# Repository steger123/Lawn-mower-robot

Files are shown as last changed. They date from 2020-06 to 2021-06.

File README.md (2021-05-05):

# Lawn-mower-robot


## The main purpose of the project:

**Create a general, affordable, computational platform, which can be used for small & medium size robots.**

The navivation can be: fully maunal, semi and full autonomouse.
The mechanical side not restricted.
As the project progressing and evolving **You can learn more and more**, **and of course, have the designs and codes for free.**

## Software:

### BASE:
Mission Planner: C#
https://github.com/steger123/Lawn-mower-robot/tree/master/03_Software%20codes/02_C%23_Mission%20planner

### ROVER:
Main MCU : C++ (Arduino)
https://github.com/steger123/Lawn-mower-robot/tree/master/03_Software%20codes/01_C%2B%2B_Arduino/01_Rover/Test_Motor_v12

AI: Python (Jetson NANO)
https://github.com/steger123/Lawn-mower-robot/tree/master/03_Software%20codes/03_Python_AI_Jetson%20Nano/01_myOpenCV

### ROVER Electronic boards:
1. Arduino MEGA later Shieldbuddy TC375 (It has 3 cores !)
2. Custom made shield, sitting on the Arduino MEGA to have enough space for connectors (4xseial, 4xSPI, 3xI2C, buttons, 3xultrasonic sensos, volt & ampere meter etc.).
3. GPS: 2 x GNSS modules with RTK / Xbee. More here: https://github.com/steger123/Lawn-mower-robot/issues/8
5. Base's RTK: simpleRTK2Blite from Ardusimple or GPS Development Tools SparkFun GPS-RTK-SMA Breakout - ZED-F9P
6. Rovers RTK: RTK+INS simpleRTK2B-F9R V3 from Ardusimple or SparkFun Accessories SparkFun GPS-RTK Dead Reckoning Breakout - ZED-F9R
7. Motor controllers: 2x DC
8. RF radio: for additional Base to Rover and back communication (remote controll, getting sensor date from rover to mission control software).
9. Jetson Nano with normal webcam. Communicating via serial port to the MEGA (detect plant diseases, following plant line)
10. Sensors on the shield (utlrasonoic distance, battery volt, curret mesuring, rain etc.)

## Body:
As you like. In scouting for example: 1m x 1m x 0.5m

## Wheels:
As you like. In scouting for example: driven 280 mm in diamteter + castor wheels.
it can be smoot like a bicycle or thick lugs like on a tractor tire (good grippong during scouting on the field).

## Engine/motor:
As you like. In scouting for example: 2x 50W DC motors with encoders. 50 rpm

## Transmission:
As you like. In scouting for example: plannetary gerabox.

## Collaboration (software, electronic hardware, new PCB/shield, mechanical parts etc.):
If You like to join, please contact me:
andras.steger@protonmail.com

More information:
https://github.com/steger123/Lawn-mower-robot/wiki

## Latest news:
https://twitter.com/StegerAndras

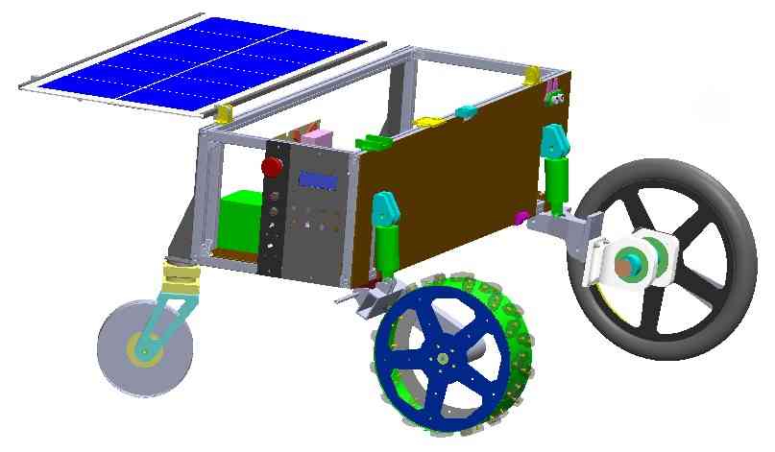
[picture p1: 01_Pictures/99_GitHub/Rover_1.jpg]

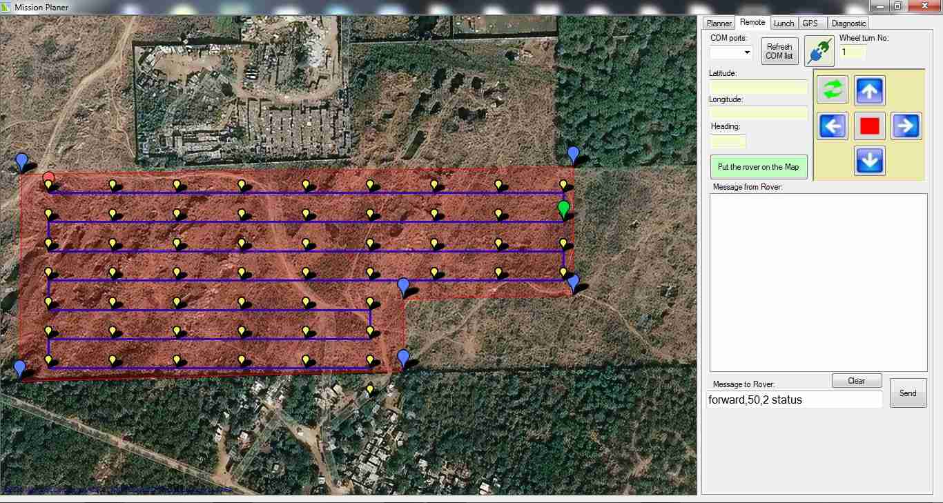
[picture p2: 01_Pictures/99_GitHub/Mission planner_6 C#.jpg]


Custom robot rover shield for Arduino MEGA or ShieldBuddy TC375:
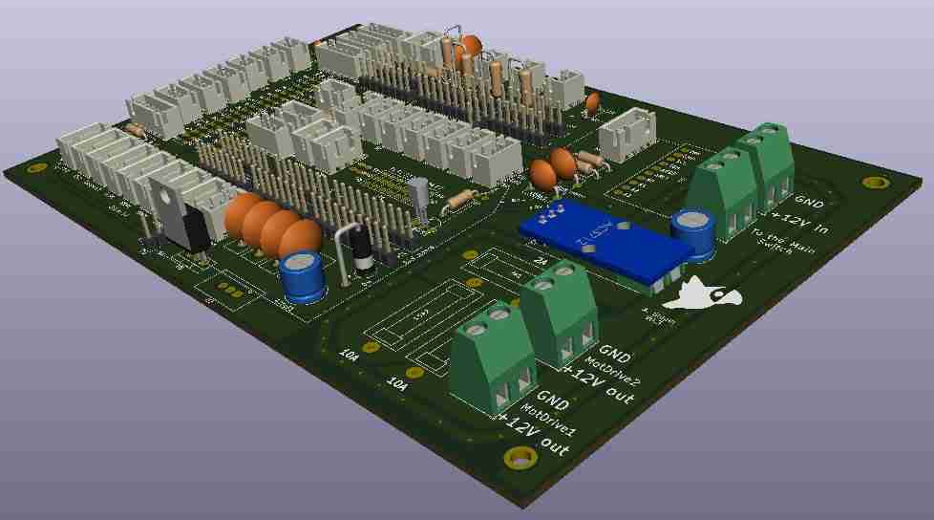
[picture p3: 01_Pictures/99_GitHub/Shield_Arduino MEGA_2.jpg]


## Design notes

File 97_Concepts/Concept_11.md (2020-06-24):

# Lawn-mower-robot
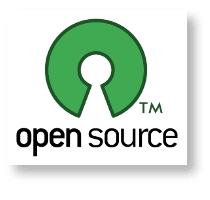
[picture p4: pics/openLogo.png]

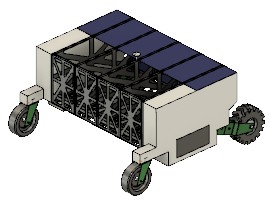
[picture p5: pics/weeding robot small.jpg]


Project parameters:

## Body:
1. Size: approx. 600x400mm
2. Total weight: max 20 kg.
3. Material: 20x20 aluminum profiles for less weight and versatility.
https://robokits.co.in/mechanical-parts/aluminium-profile-accessories/black-anodized-industrial-aluminum-alloy-2020b-profile
4.	Design platform: in AutoCAD Fusion 360

## Driven Wheels (2 pcs):
1.	Size: 10-13 inch
2.	Weight: max. 500 g/pc
3.	Material: 3D printed from PETG (PLA have less strength & fatigue).
4.	Design platform: in AutoCAD Fusion 360

## Not driven wheels (2 pcs):
1.	Caster wheel.

## Transmission:
1.	Motor: 2 pcs ODrive with encoder (DUAL SHAFT MOTOR - D6374 150KV)
https://odriverobotics.com/shop/odrive-custom-motor-d6374-150kv
2.	Motor Driver: 1pcs ODrive v3.6
https://odriverobotics.com/shop/odrive-v36
3.	Gear box with timing spokets and belt.

## Electronic:
1.	Jetson Nano
2.  Camera
3.	Route planning: GPS and real kinematics

## Software:
1. Python
2. TensorFlow, PyTorch
The software have to ensure object recognition, obstacle avoidance and route planning.

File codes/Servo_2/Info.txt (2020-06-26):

https://www.youtube.com/watch?v=9jcEwn7GzNs
https://github.com/adafruit/Adafruit_Python_PCA9685

To install the library from source (recommended) run the following commands
 on a Raspberry Pi or other Debian-based OS system:
Enable I2C on RP ! ($ sudo raspi-config)

sudo apt-get install git build-essential python-dev
cd ~     #may be not reqired
git clone https://github.com/adafruit/Adafruit_Python_PCA9685.git
cd Adafruit_Python_PCA9685
sudo python setup.py install    # for python 2
sudo python3 setup.py install	# for python 3

Program:
# Simple demo of of the PCA9685 PWM servo/LED controller library.
# This will move channel 0 from min to max position repeatedly.
# Author: Tony DiCola
# License: Public Domain
from __future__ import division
import time

# Import the PCA9685 module.
import Adafruit_PCA9685

# Uncomment to enable debug output.
#import logging
#logging.basicConfig(level=logging.DEBUG)

# Initialise the PCA9685 using the default address (0x40).
pwm = Adafruit_PCA9685.PCA9685()

# Alternatively specify a different address and/or bus:
#pwm = Adafruit_PCA9685.PCA9685(address=0x41, busnum=2)

# Configure min and max servo pulse lengths
servo_min = 150  # Min pulse length out of 4096
servo_max = 600  # Max pulse length out of 4096

# Helper function to make setting a servo pulse width simpler.
def set_servo_pulse(channel, pulse):
    pulse_length = 1000000    # 1,000,000 us per second
    pulse_length //= 60       # 60 Hz
    print('{0}us per period'.format(pulse_length))
    pulse_length //= 4096     # 12 bits of resolution
    print('{0}us per bit'.format(pulse_length))
    pulse *= 1000
    pulse //= pulse_length
    pwm.set_pwm(channel, 0, pulse)

# Set frequency to 60hz, good for servos.
pwm.set_pwm_freq(60)

print('Moving servo on channel 0, press Ctrl-C to quit...')
while True:
    # Move servo on channel O between extremes.
    pwm.set_pwm(0, 0, servo_min)
    time.sleep(1)
    pwm.set_pwm(0, 0, servo_max)
    time.sleep(1)

# Move servo on channel 1 between extremes.
    pwm.set_pwm(1, 0, servo_min)
    time.sleep(1)
    pwm.set_pwm(1, 0, servo_max)
    time.sleep(1)

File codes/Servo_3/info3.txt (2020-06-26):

https://learn.adafruit.com/16-channel-pwm-servo-driver?view=all

#sudo apt-get install ...
sudo pip install Adafruit-Blinka
sudo pip install adafruit-circuitpython-pca9685
sudo pip install adafruit-circuitpython-servokit

Program:
# Simple test for a standard servo on channel 0 and
# a continuous rotation servo on channel 1.

import time
from adafruit_servokit import ServoKit
 
# Set channels to the number of servo channels on your kit.
kit = ServoKit(channels=16)  # 8 for FeatherWing, 16 for Shield/HAT/Bonnet.
 
kit.servo[0].angle = 180      #Set the angle to 180, one extreme of the range
kit.continuous_servo[1].throttle = 1      #start the continuous rotation servo connected to channel 1 to full throttle forwards
# kit.continuous_servo[1].throttle = 0.5 To set half throttle, use a decimal
time.sleep(1)
kit.continuous_servo[1].throttle = -1     #start the continuous rotation servo connected to channel 1 to full reverse throttle

time.sleep(1)

kit.servo[0].angle = 0   #Return the servo to 0 degrees
kit.continuous_servo[1].throttle = 0    # stop continuous rotation servo movement

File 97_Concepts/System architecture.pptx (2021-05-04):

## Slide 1

System architecture
Robot mover
Main purpose: scouting for pant diseases on the agricultural fields

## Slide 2

BASE laptop/PC

ROVER
Robot mower
12V, 2x DC motors
Arduino MEGA + Custom shield

Radio
remote + send sensor data

GPS board with RTK

GNSS multiband antenna

XBee to receive RTK messages from BASE

Sensors:
- ultrasonic distance, wheel encoder,
current, battery voltage etc.
- AI (Jetson Nano + Python)

Misson planner in C# VS 2013

Radio
for remote (1km) + sensor data

GPS board with RTK

GNSS multiband antenna

XBee to send RTK messages (RTCM)

## How AI can be integrated in the mower ?

- The main purpose of the robot mower is to scout the plans, searching/warning for early disease.
- So Jetson Nano can be used for image detection. Start here: https://www.youtube.com/watch?v=bcM5AQSAzUY
https://github.com/dusty-nv/jetson-inference/
Need:
  - Jetson Nano, but go for 4GB version(not 2GB !)
  - Above link show how easy to make it.
  - Image AI have 3 main areas (classification, detection & segmentation)
    - We need the detection part: As the rower moving on the field and let say making pictures after every 10m. On those pictures to be detected is there any disease.
    - For this we can use already made data set or make our own: https://github.com/dusty-nv/jetson-inference/blob/master/docs/pytorch-collect-detection.md
  - Make the Jetson Nano portable, so You can put on the rower and communicate via serial port to Ardunio MEGA. The MEGA can send the data back to the BASE via radio and visualize the data on a map or the Nano can store them.

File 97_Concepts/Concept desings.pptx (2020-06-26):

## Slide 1

?

A

B

C

Fixed wheel

Turnable wheel

Heading

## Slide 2

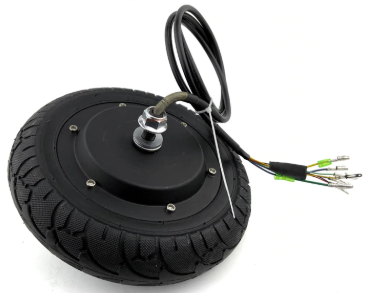
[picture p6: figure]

Brush less
Hub motor

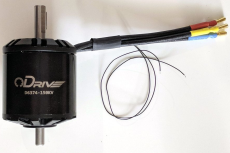
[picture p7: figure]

Brush less
normal dual shaft

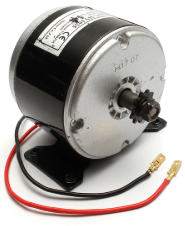
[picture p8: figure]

Brushed
motor

?

A

B

C

(feilds highlighted in blue are inputs) | kv | Max current | Max voltage | price | Weight | Link | Torque | No-load speed | | | Force | Acceleration | Time to base speed | distance to base speed | Power at base speed | Base speed kinetic energy | Encoder freq. (base speed)
| rpm/v | A | V | USD | g | | Nm | rpm | rad/s | m/s | N | m/s^2 | ms | mm | W | J | kHz

ODrive Robotics D6374 - 150kv | 150 | 70 | 48 | 99 | 890 | | 3.86 | 5760 | 603.19 | 5.76 | 404.15 | 134.87 | 42.71 | 123.00 | 2328 | 31.52 | 196.608

70*48=3360W

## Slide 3

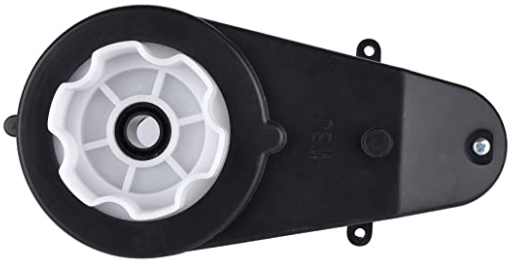
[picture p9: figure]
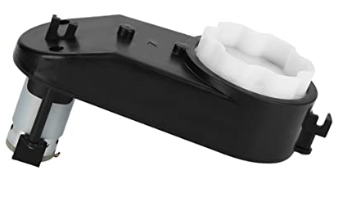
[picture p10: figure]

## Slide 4

Electric block diagram

Battery

Controller

Jetson Nano

Solar panel

Pixhawk
Flight controller

Electronic compass
Acceleration

Not sure

Camera

10W

Motor controller

Motors

GPS

10W

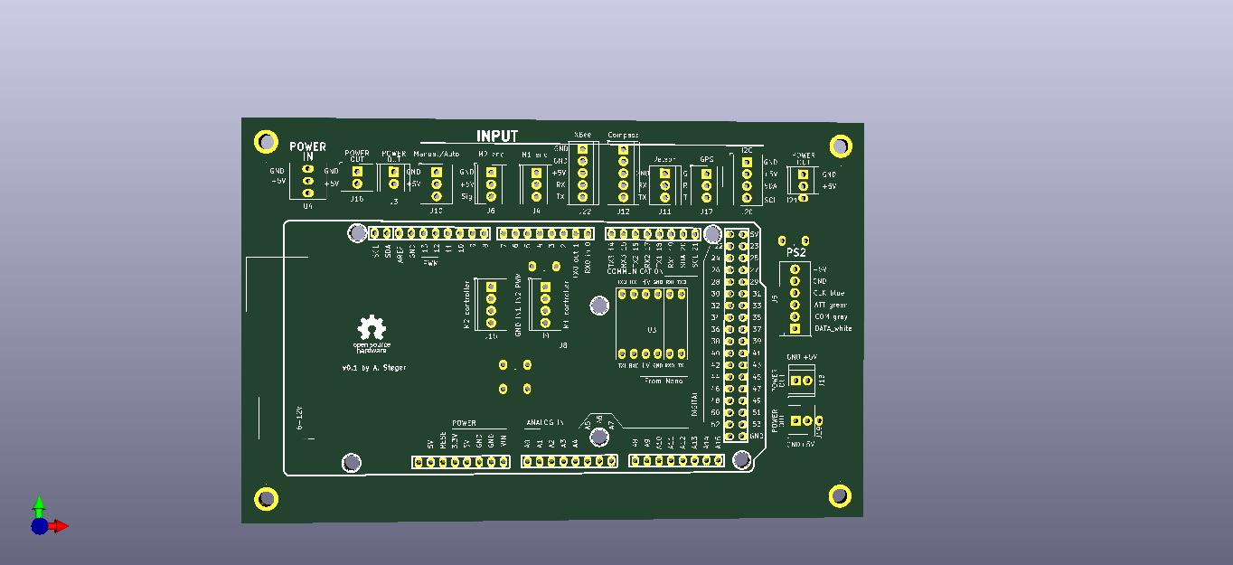
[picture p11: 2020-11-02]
02_Electronic desings/Pictures/PCB_1.jpg

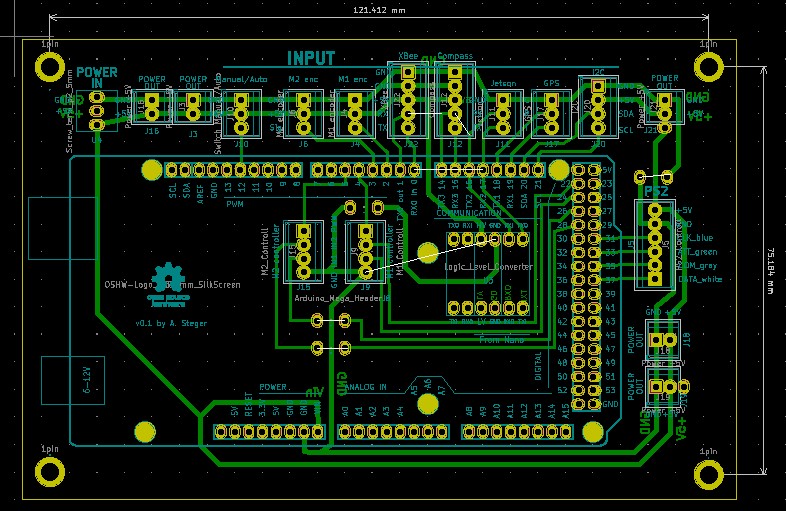
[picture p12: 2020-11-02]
02_Electronic desings/Pictures/PCB_00.jpg

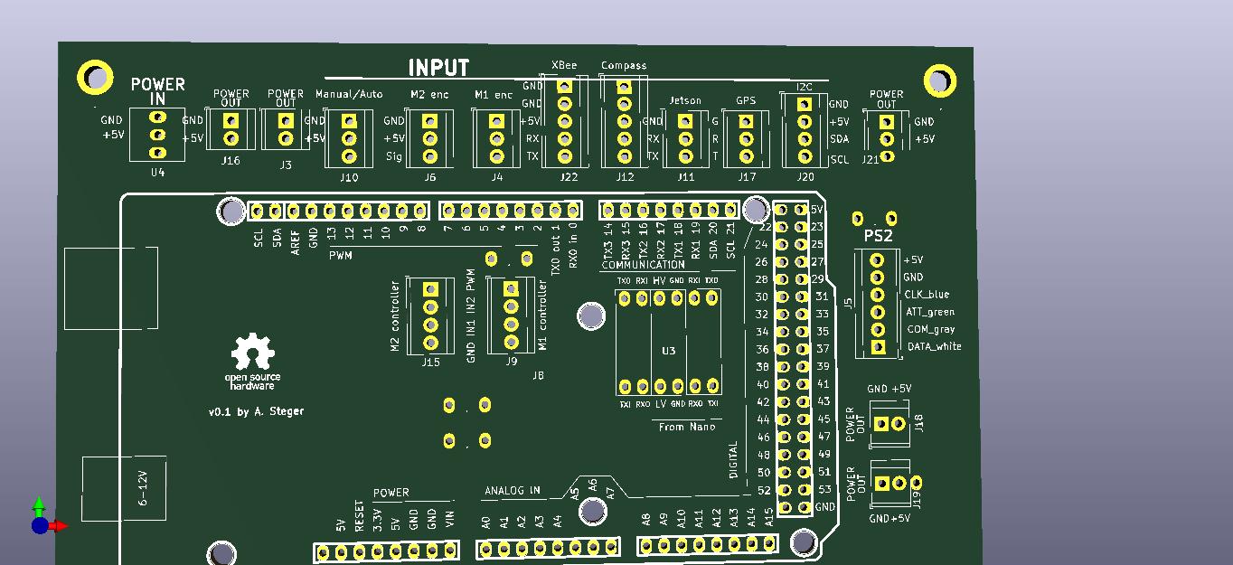
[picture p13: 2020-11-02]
02_Electronic desings/Pictures/PCB_0.jpg

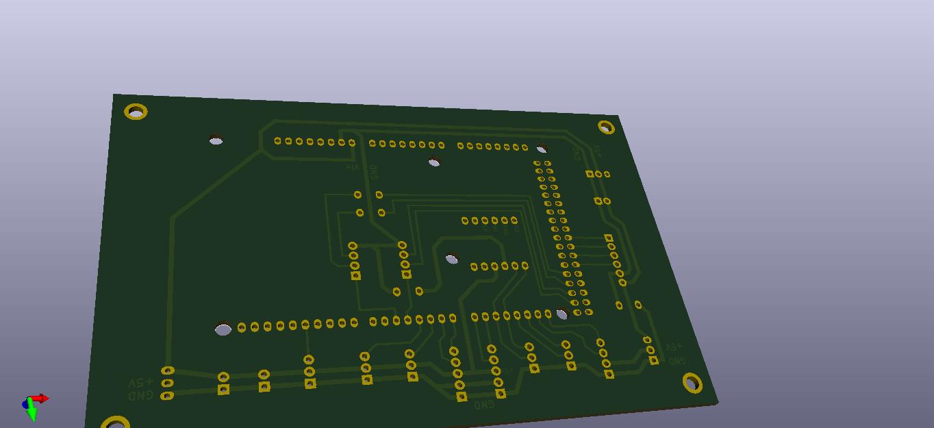
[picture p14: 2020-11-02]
02_Electronic desings/Pictures/PCB_3.jpg

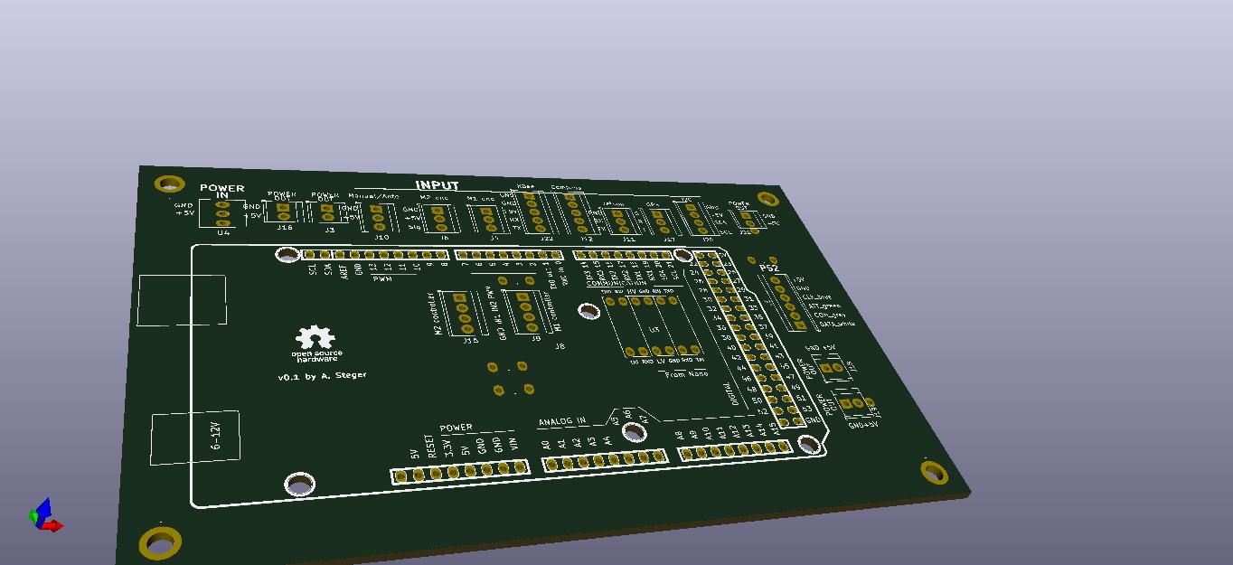
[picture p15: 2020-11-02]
02_Electronic desings/Pictures/PCB_2.jpg

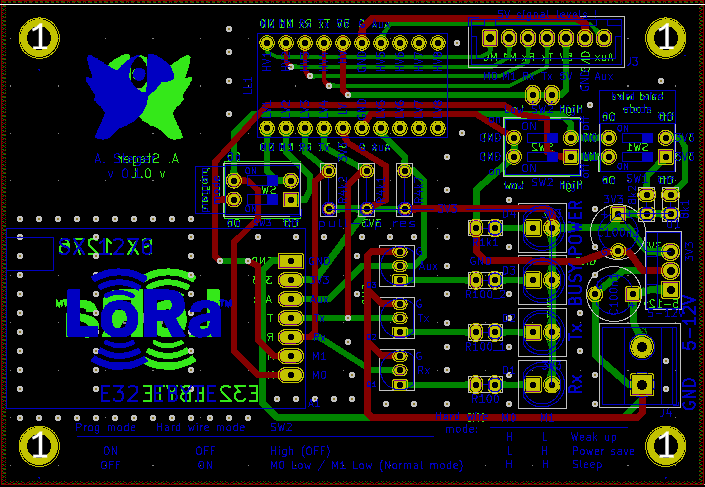
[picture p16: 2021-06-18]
02_Electronic desings/PCB LoRa 32/Images & Schematic/PCB connections.png

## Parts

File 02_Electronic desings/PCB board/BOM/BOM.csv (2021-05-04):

Item Description | Manufacturer part No | Name | Package Designator | Quantity
Voltage References PREC MICROPWR SHUNT VLTG REF | LM4040AIZ-4.1/NOPB | Texas Instruments | TO-92-3 | 3
Voltage References 2.5V 0.2% SHUNT REFERENCE | LM4040B25FTA | Diodes Incorporated | SOT-23-3 | 3
Voltage References VREG Shunt Reference SSOT23 T&R 3K | LM4040B41FTA | Diodes Incorporated | SOT-23-3 | 3
Infineon Technologies AURIX™ ShieldBuddyTC375 Development Board | KITA2GTC375ARDSBTOBO1 | Infineon | Development Board | 2
Non-Isolated DC/DC Converters 6.5-36Vin 5V 2A SIP switching regulator | TSR 2-2450 | TRACO Power | SIP-3 | 3
Non-Isolated DC/DC Converters 6-36Vin 3.3Vout 1A SIP Non-Iso | TSR 1-2433E | TRACO Power | SIP-3 | 3
Schottky Diodes & Rectifiers PEC/SB240/TB/52mm/RoHS/3K/DO-15/SKY/AXIAL/SB-20/SB20-QI01/PJ/// | SB240_AY_10001 | Panjit | DO-15-2 | 5
Schottky Diodes & Rectifiers 3A 40V | MBRA340T3G | ON Semiconductor | SMA (DO-214AC) | 5
Multilayer Ceramic Capacitors MLCC - SMD/SMT 10V 0.1uF X8R 1210 1% AEC-Q200 | C1210C104F8HACAUTO | KEMET | SMD/SMT | 10
Tantalum Capacitors - Solid SMD 16V 47uF 20% 2917 ESR = .9 Ohm | TAJD476M016UNJV | AVX | SMD/SMT | 5
Ferrite Beads 0603 10 OHM | BLM18BA100SN1D | Murata | SMD/SMT | 5
Thick Film Resistors - SMD 51K OHM 1% 1/4W TC100 | CMP0603AFX-5102ELF | Bourns | SMD/SMT | 5

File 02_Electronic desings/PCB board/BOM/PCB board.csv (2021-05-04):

Id | Designator | Package | Quantity | Designation | Supplier and ref
1 | .,. | 1_pin | 2 | .
2 | Button3 | JST_XH_B2B-XH-A_1x02_P2.50mm_Vertical | 1 | TestBtn3
3 | Button2 | JST_XH_B2B-XH-A_1x02_P2.50mm_Vertical | 1 | TestBtn2
4 | Button1 | JST_XH_B2B-XH-A_1x02_P2.50mm_Vertical | 1 | TestBtn1
5 | D4 | D_5W_P5.08mm_Vertical_AnodeUp | 1 | 1N4001
6 | 100n2,100n8,100n7,100n6,100n1 | C_Disc_D10.5mm_W5.0mm_P5.00mm | 5 | 100nF
7 | U5 | TO-220-3_Vertical | 1 | LM7803_TO220
8 | U7 | Traco_TSR2 | 1 | LM7805_TO220
9 | S1 | TO-92 | 1 | LM4040 4.1V
10 | G***,G*** | parrot | 2 | LOGO
11 | 10k3,10k1,10k2 | R_Axial_DIN0207_L6.3mm_D2.5mm_P10.16mm_Horizontal | 3 | 10k
12 | 470uF1 | C_Radial_D8.0mm_H7.0mm_P3.50mm | 1 | 470uF
13 | 5V,3V3 | Heatsink | 2 | Heatsink
14 | J6,J5,J7,J9,J10,J11,J15,J16,J18,J19 | Terminal_p8 | 10 | .
15 | PS2 | JST_XH_B6B-XH-A_1x06_P2.50mm_Vertical | 1 | PS2_Controll
16 | ULeft1 | JST_XH_B4B-XH-A_1x04_P2.50mm_Vertical | 1 | Ultrasonic Left
17 | URight1,UCenter1 | JST_XH_B4B-XH-A_1x04_P2.50mm_Vertical | 2 | Ultrason_Right
18 | U3 | ASC712 | 1 | ACS712_30A
19 | U6 | ADS1115 | 1 | ADS1115
20 | 100uF1 | C_Radial_D8.0mm_H7.0mm_P3.50mm | 1 | 100 uF
21 | MotDrive2 | TerminalBlock_Phoenix_MKDS-1,5-2-5.08_1x02_P5.08mm_Horizontal | 1 | 12V Mot2 OUT
22 | .,.,.,. | 1pin | 4 | 1pin
23 | 22k1 | R_Axial_DIN0207_L6.3mm_D2.5mm_P10.16mm_Horizontal | 1 | 22k
24 | 47k1 | R_Axial_DIN0309_L9.0mm_D3.2mm_P12.70mm_Horizontal | 1 | 47k1
25 | J12,J13 | Terminal_p36 | 2 | .
26 | J14,J17 | Terminal_p10 | 2 | .
27 | SW1 | TerminalBlock_Phoenix_MKDS-1,5-2-5.08_1x02_P5.08mm_Horizontal | 1 | SW_DIP_x01
28 | U4 | TerminalBlock_Phoenix_MKDS-1,5-2-5.08_1x02_P5.08mm_Horizontal | 1 | ST
29 | Pullup1 | R_Axial_DIN0207_L6.3mm_D2.5mm_P10.16mm_Horizontal | 1 | 4k7
30 | 2k2 | R_Axial_DIN0309_L9.0mm_D3.2mm_P5.08mm_Vertical | 1 | 2k2
31 | 4k7 | R_Axial_DIN0309_L9.0mm_D3.2mm_P5.08mm_Vertical | 1 | 4k7
32 | 6k8 | R_Axial_DIN0309_L9.0mm_D3.2mm_P5.08mm_Vertical | 1 | 6k8
33 | MotDrive1 | TerminalBlock_Phoenix_MKDS-1,5-2-5.08_1x02_P5.08mm_Horizontal | 1 | 12V Mot1 OUT
34 | 100n5,100n4 | C_Disc_D7.5mm_W5.0mm_P7.50mm | 2 | 100n
35 | P1,P2,P3,P4,P5,P6,P7,P8 | Terminal_p3 | 8 | HEADER_3
36 | 2A1 | Fuse | 1 | 2A
37 | 15A1,15A2 | Fuse | 2 | 15A1
38 | D1,D2,D3,A6,A7,A1,A2,A3,A4,A5 | JST_XH_B3B-XH-A_1x03_P2.50mm_Vertical | 10 | s1
39 | Temp1 | JST_XH_B3B-XH-A_1x03_P2.50mm_Vertical | 1 | Temp sensor
40 | Rain1 | JST_XH_B4B-XH-A_1x04_P2.50mm_Vertical | 1 | Rain Sensor
41 | Current1 | JST_XH_B3B-XH-A_1x03_P2.50mm_Vertical | 1 | Current sensor
42 | J2 | JST_XH_B4B-XH-A_1x04_P2.50mm_Vertical | 1 | ST_01x04
43 | MB_Control1 | JST_XH_B4B-XH-A_1x04_P2.50mm_Vertical | 1 | MB_Control
44 | MA_Control1 | JST_XH_B4B-XH-A_1x04_P2.50mm_Vertical | 1 | MA_Control
45 | MA_enc1 | JST_XH_B3B-XH-A_1x03_P2.50mm_Vertical | 1 | MA_enc1
46 | MB_enc1 | JST_XH_B3B-XH-A_1x03_P2.50mm_Vertical | 1 | MB encoder
47 | Man/Auto1 | JST_XH_B3B-XH-A_1x03_P2.50mm_Vertical | 1 | Switch Manual/Auto
48 | GPS1 | JST_XH_B3B-XH-A_1x03_P2.50mm_Vertical | 1 | GPS
49 | GSM1 | JST_XH_B3B-XH-A_1x03_P2.50mm_Vertical | 1 | GSM
50 | LCD1 | JST_XH_B4B-XH-A_1x04_P2.50mm_Vertical | 1 | LCD display
51 | Compass1 | JST_XH_B4B-XH-A_1x04_P2.50mm_Vertical | 1 | Compass
52 | I2C1 | JST_XH_B4B-XH-A_1x04_P2.50mm_Vertical | 1 | I2C
53 | XBee1 | JST_XH_B3B-XH-A_1x03_P2.50mm_Vertical | 1 | XBee
54 | 1u2,1u3 | C_Disc_D3.8mm_W2.6mm_P2.50mm | 2 | 1u
55 | 1u1 | C_Disc_D5.0mm_W2.5mm_P5.00mm | 1 | 1u
56 | SD1 | JST_XH_B6B-XH-A_1x06_P2.50mm_Vertical | 1 | SD card
57 | RTC1 | JST_XH_B4B-XH-A_1x04_P2.50mm_Vertical | 1 | RTC
58 | 1k1 | R_Axial_DIN0207_L6.3mm_D2.5mm_P10.16mm_Horizontal | 1 | 1k
59 | J1,J3 | Terminal_p2 | 2 | HEADER_2

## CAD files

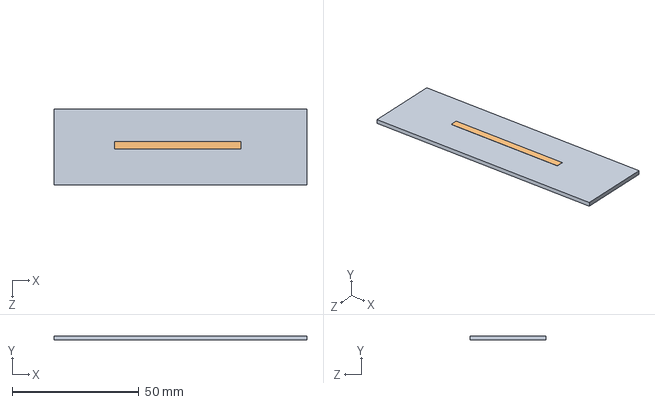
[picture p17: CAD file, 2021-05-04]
02_Electronic desings/PCB board/FEA/Assem2.SLDASM
100.0 x 1.67 x 30.0 mm
PCB
Strip

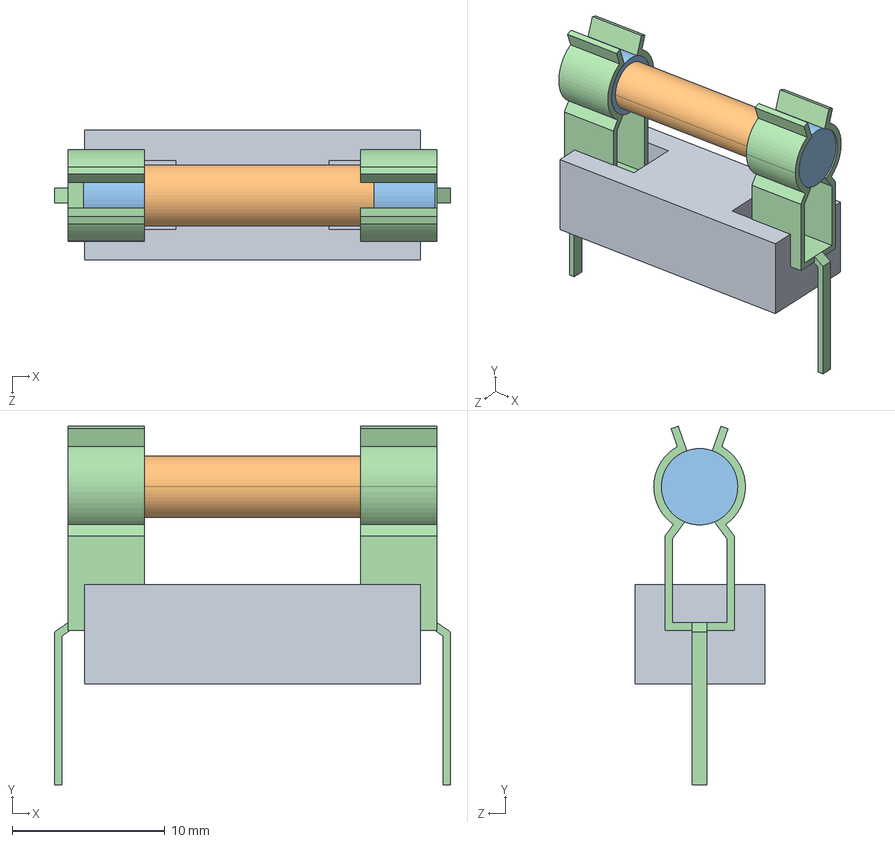
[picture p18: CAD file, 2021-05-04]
02_Electronic desings/PCB board/3Dmodels/Assy fuse_1.STEP
25.9 x 23.5 x 8.50 mm
base
fuse
contact x 2
Electrode x 2

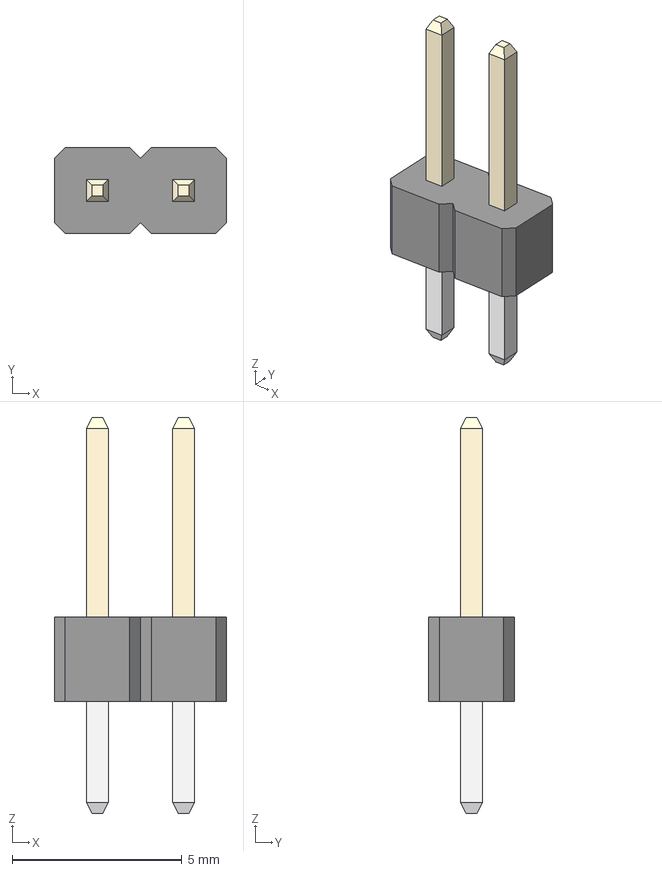
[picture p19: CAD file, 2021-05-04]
02_Electronic desings/PCB board/3Dmodels/1x2.iges
5.08 x 2.54 x 11.7 mm

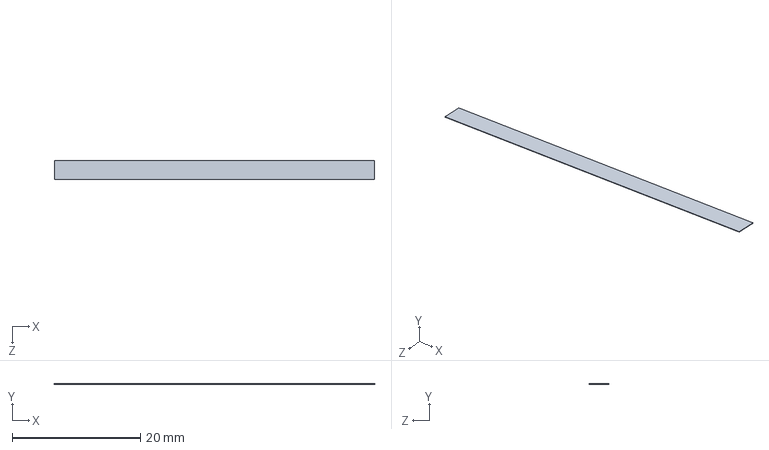
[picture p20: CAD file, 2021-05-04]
02_Electronic desings/PCB board/FEA/Strip.SLDPRT
50.0 x 0.07 x 3.00 mm

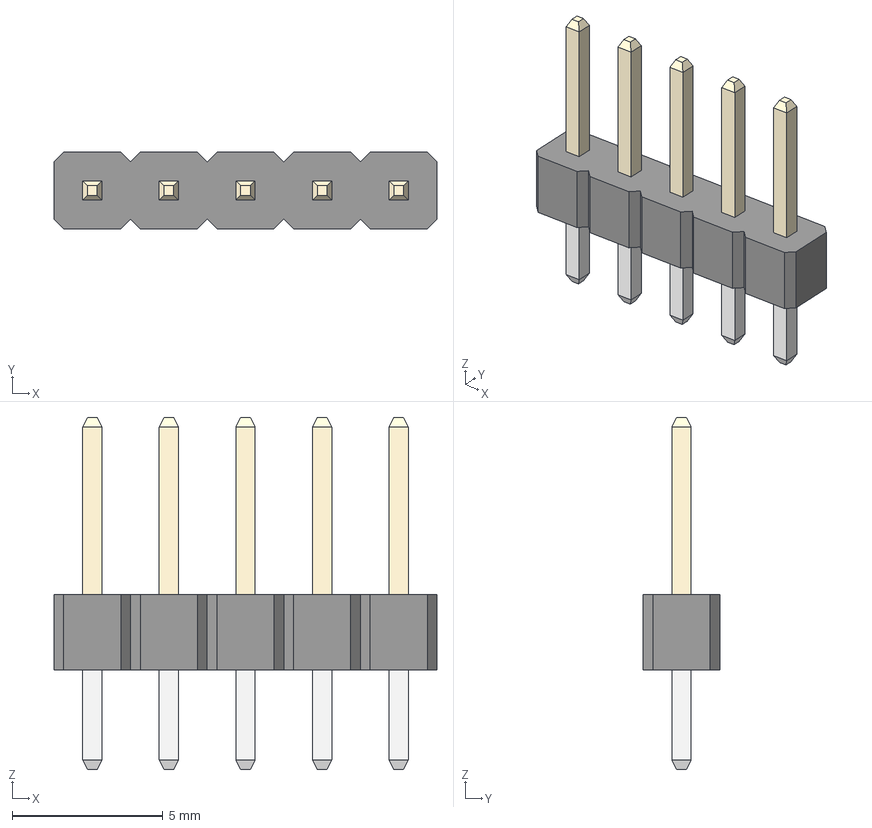
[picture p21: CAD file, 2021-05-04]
02_Electronic desings/PCB board/3Dmodels/1x5 TH Vert 100mil.step
12.7 x 2.54 x 11.7 mm

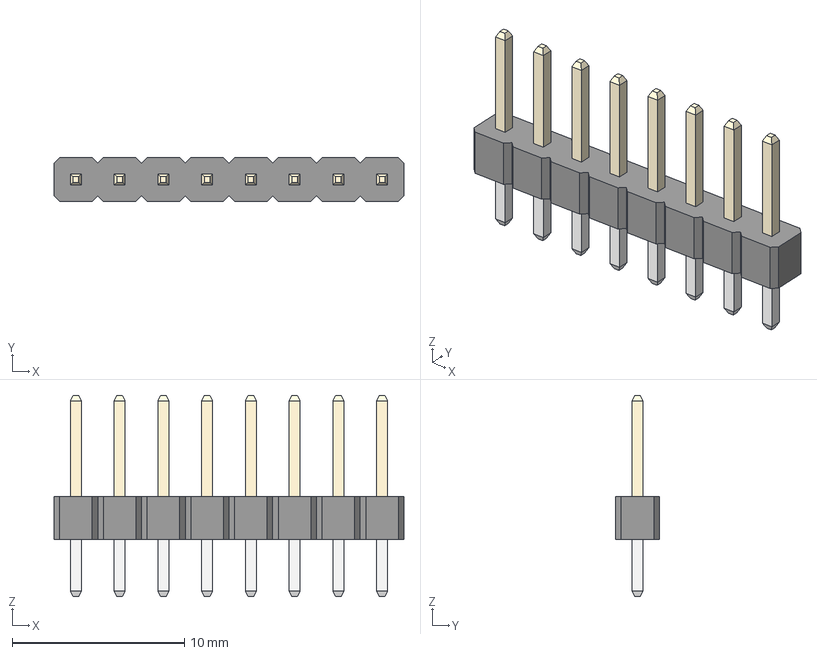
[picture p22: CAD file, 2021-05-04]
02_Electronic desings/PCB board/3Dmodels/1x8 TH Vert 100mil.step
20.3 x 2.54 x 11.7 mm

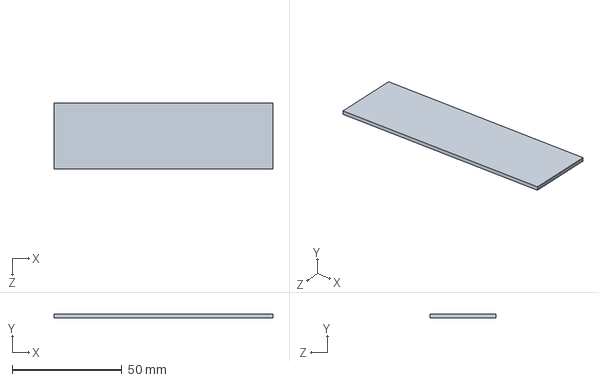
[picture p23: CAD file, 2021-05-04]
02_Electronic desings/PCB board/FEA/PCB.SLDPRT
100.0 x 1.60 x 30.0 mm

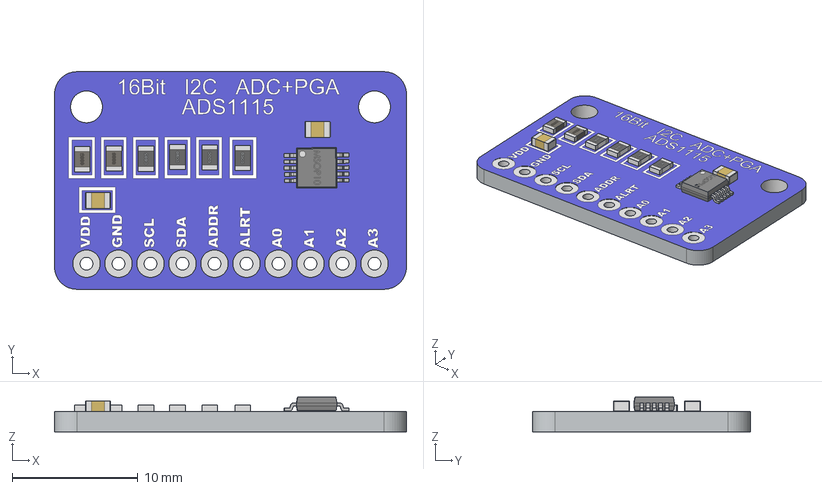
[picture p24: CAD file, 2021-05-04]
02_Electronic desings/PCB board/3Dmodels/ADS1115.stp
27.9 x 17.3 x 2.74 mm
ADS1115
0805 Capacitor x 2
0805 Inductor x 2
0805 Resistor x 4
MSOP10

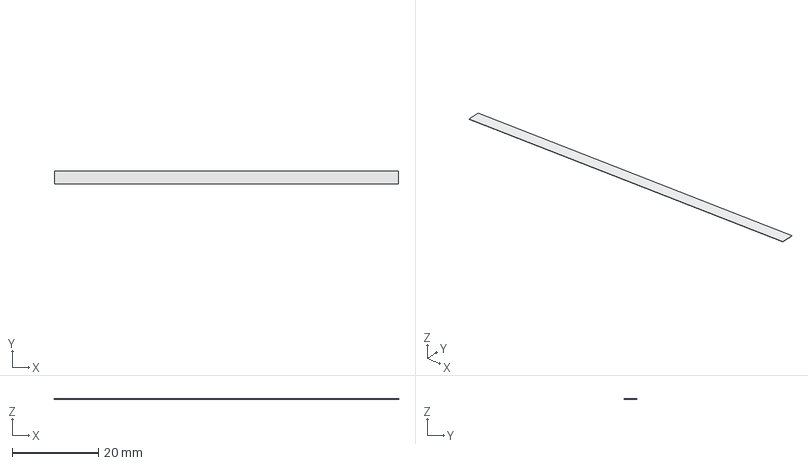
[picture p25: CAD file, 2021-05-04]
02_Electronic desings/PCB board/FEA/strip_1.FCStd
80.0 x 3.00 x 0.07 mm

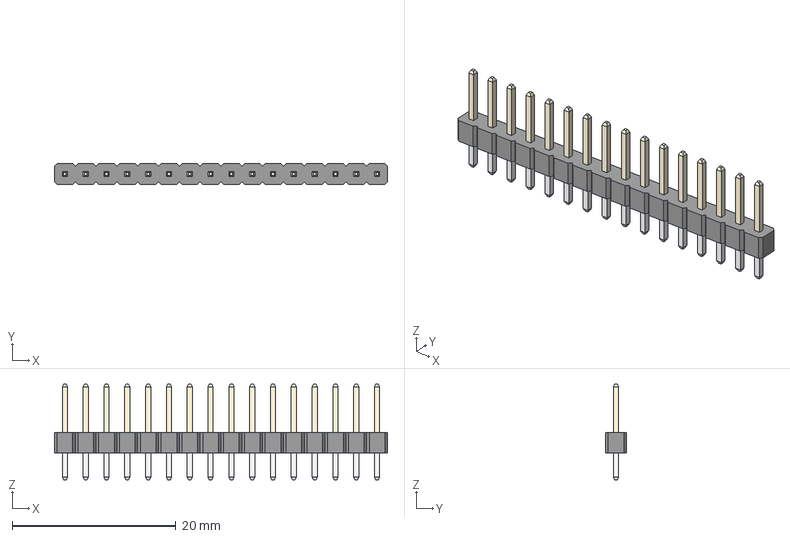
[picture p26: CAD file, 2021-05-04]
02_Electronic desings/PCB board/3Dmodels/1x16 TH Vert 100mil.step
40.6 x 2.54 x 11.7 mm

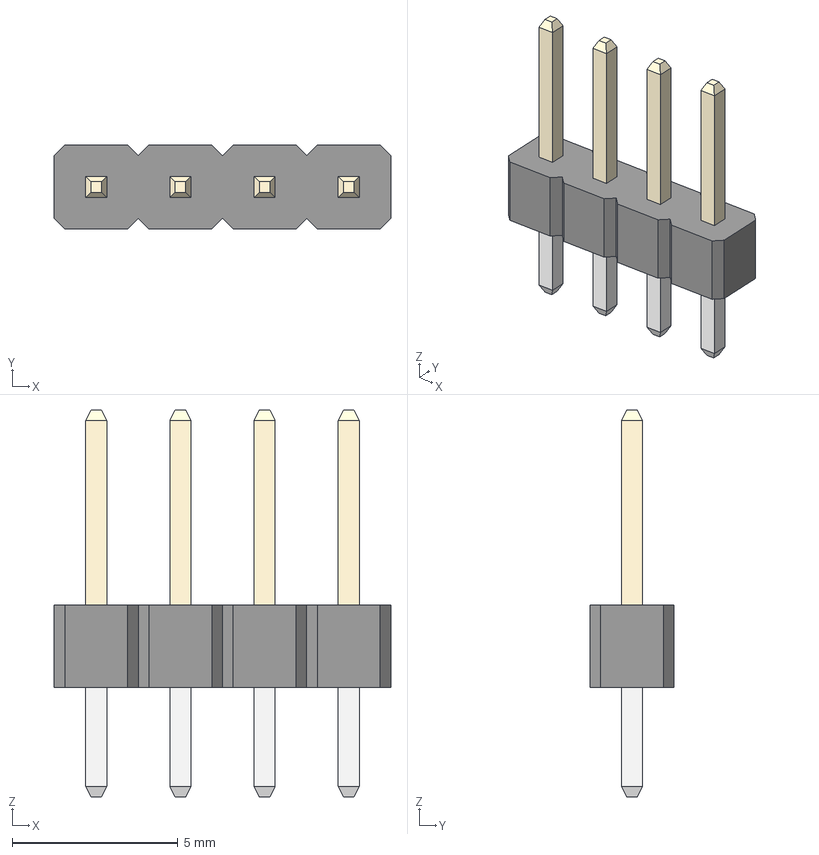
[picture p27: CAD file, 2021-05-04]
02_Electronic desings/PCB board/3Dmodels/1x4 TH Vert 100mil.step
10.2 x 2.54 x 11.7 mm

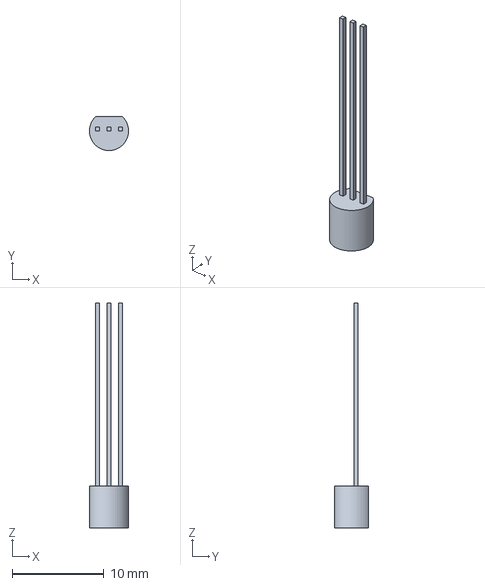
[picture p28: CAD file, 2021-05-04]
02_Electronic desings/PCB board/3Dmodels/TO92.step
4.28 x 3.72 x 24.6 mm

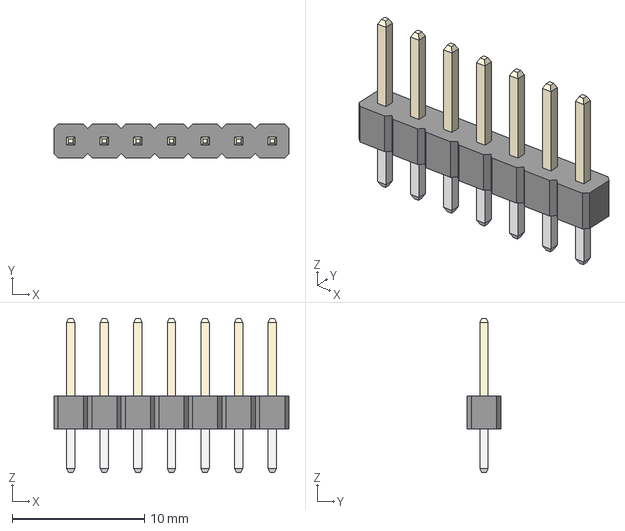
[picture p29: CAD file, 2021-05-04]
02_Electronic desings/PCB board/3Dmodels/1x7 TH Vert 100mil.step
17.8 x 2.54 x 11.7 mm

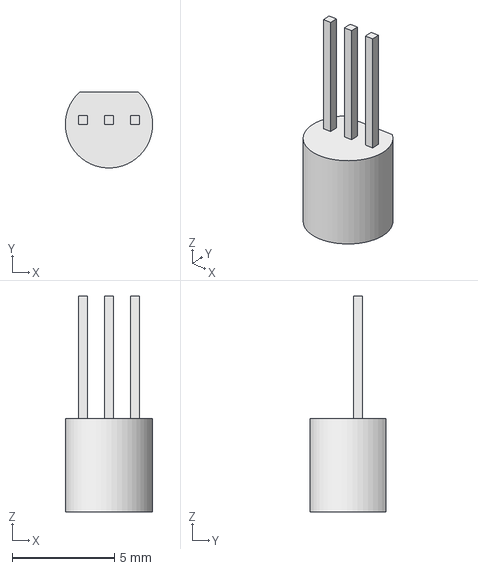
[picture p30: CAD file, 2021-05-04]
02_Electronic desings/PCB board/3Dmodels/TO92_2.step
4.28 x 3.72 x 10.6 mm

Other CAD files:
02_Electronic desings/PCB board/3Dmodels/Assy fuse_2.STEP
02_Electronic desings/PCB board/FEA/strip_0.FCStd
02_Electronic desings/PCB board/FEA/strip_2.FCStd
02_Electronic desings/PCB board/3Dmodels/1x9 TH Vert 100mil.step
02_Electronic desings/PCB board/3Dmodels/1x1 TH Vert 100mil.iges
02_Electronic desings/PCB board/3Dmodels/1x1 TH Vert 100mil.step
02_Electronic desings/PCB board/3Dmodels/1x10 TH Vert 100mil.iges
02_Electronic desings/PCB board/3Dmodels/1x10 TH Vert 100mil.step
02_Electronic desings/PCB board/3Dmodels/1x11 TH Vert 100mil.iges
02_Electronic desings/PCB board/3Dmodels/1x11 TH Vert 100mil.step
02_Electronic desings/PCB board/3Dmodels/1x12 TH Vert 100mil.iges
02_Electronic desings/PCB board/3Dmodels/1x12 TH Vert 100mil.step
02_Electronic desings/PCB board/3Dmodels/1x13 TH Vert 100mil.iges
02_Electronic desings/PCB board/3Dmodels/1x13 TH Vert 100mil.step
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

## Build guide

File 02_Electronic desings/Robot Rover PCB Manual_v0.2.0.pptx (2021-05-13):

## Robot rover shield

For Arduino or Keyestudio MEGA 2560 , Due , Hitex ShiledBuddy TC275 or TC375, Adafruit ntral M4 Express

## Ports

B

A

C

D

## A – Section (navigation sensors)

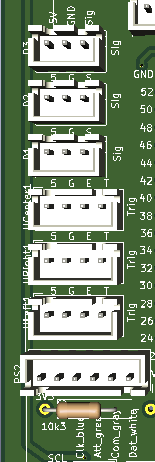
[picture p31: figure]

D3:
5V GND SIG(47)

D2:
5V GND SIG(45)

D1:
5V GND SIG(43)

Ultrasonic (CENTER):
5V GND ECHO(41) TRIGGER(39)

HC-SR04 Ultrasonic sensors:
4k7Ω & 2k7Ω Voltage divider required on ECHO pin ???

Ultrasonic (RIGHT):
5V GND ECHO(37) TRIGGER(35)

Ultrasonic (LEFT):
5V GND ECHO(33) TRIGGER(31)

PS2 controller:
3V3 GND CLK(29) ATT(27) COM(25) DATA(23)
blue green gray white

## ADUINO & Ultrasonic sensor

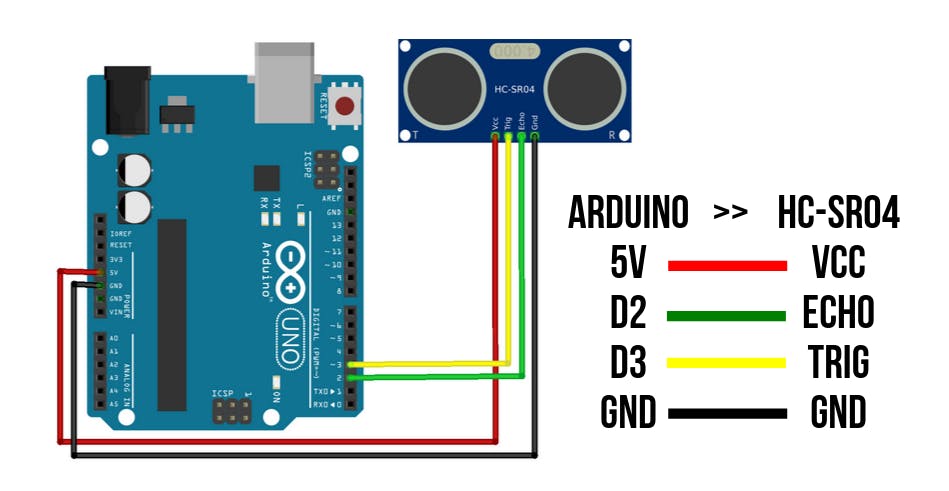
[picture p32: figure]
Ultrasonic Sensor HC-SR04 with Arduino Tutorial - Arduino Project Hub

## B – Section (SD card & analog Input)

SPI SD card:
GND 5V MISO(50) MOSI(51) SCK(52) CS(53)

A7:
SIG(A15) GND 5V

VBat:
SIG(A11)

Buttons for:
SIG(A10)

A6:
SIG(A14) GND 5V

Button:
SIG(A10)

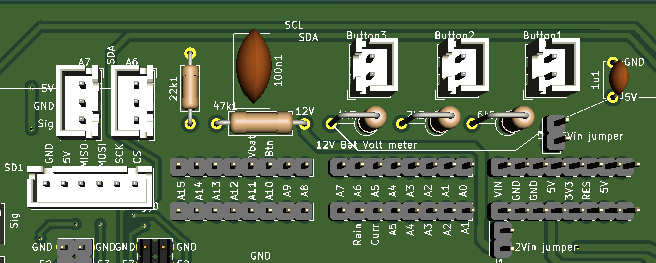
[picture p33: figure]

## C – Section (Sensors & Motor control)

Rain drop sensor:
SIG(A6) GND 5V SIG(40)

Temperature sens.:
SIG(46) GND 5V

Current sens.:
SIG(A5) GND 5V

A5 – A1:
SIG(A4 – A0) GND 5V

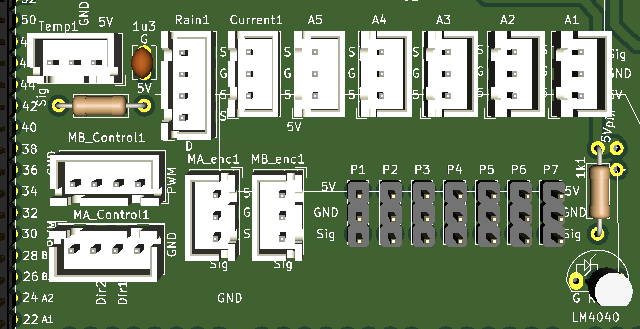
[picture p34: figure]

MB_Controll:
GND DIR_B1(28) DIR_B2(26) PWM_B(3)

MA_Controll:
GND DIR_A1(22) DIR_A2(24) PWM_A(2)

MA_Encoder:
SIG(4) GND 5V

MB_Encoder:
SIG(5) GND 5V

P1-P7:
SIG(7-13) GND 5V

## D – Section (I2C & Serial communication)

TX0 /RX0 is for Jetson Nano on normal serial connector !

(Current mearument: ADS1115
ADDR pin to GND -> 0x48)

GSM (1):
TX1 RX1 GND

GPS (2):
TX2 RX2 GND

XBEE (3):
TX3 RX3 GND

Flip in RTC the GND & 5V positions !!!:

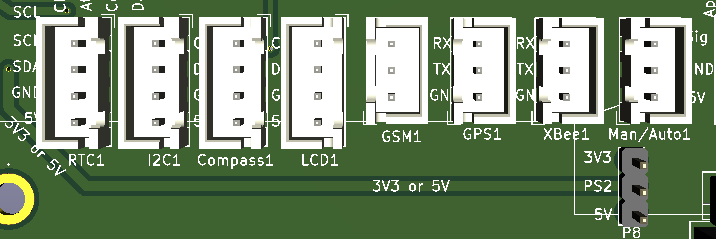
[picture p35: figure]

DS3231 RTC (0x57 I2C):
5V GND SDA SCL

BNO055 9-DOF Compass
(0x28 I2C): 5V GND SDA SCL

Maual/Auto:
5V GND SIG(6)

I2C (free I2C):
5V GND SDA SCL

LCD2004 (0x27, I2C):
5V GND SDA SCL

## Power management (for 5V MCUs)

Jumper for 5V IN
5V from buck power supply

12V IN
for 2 motors, shield & MCU

For main & safety switch

Jumper for 12V IN
(not in use)

Jumper for PS2 5V? or 3V3

5V to 3V3 regulator for PS2 only

Fuses

12V OUT
or 2 motors

12V or 24V to 5V mini buck converter. This can be replaced to 12V to 3V3 for DUE

## Power measurement

ADS1115
ACS712 Sig to ADS1115’s A3
10k/10k to ADS1115’s A2
SCL SDA GND 5V

Mesure internal ref 2.56V with separayte Arduin sketch as well ! Measure_intRefVolt.ino

10kΩ & 47kΩ (measre before soldering !) BatRs[] = voltage deivider for battery volt measurement Signal to A11

ADS1115
ADDR pin to GND -> 0x48

2x 10kΩ voltage divider for ADS1115

Current measurrment
ACS712 (30A)
5V Sig GND
Sig to ADS1115’s A3

Or connect signal
of ACS712 to A5

1kΩ & LM4040_2.5 V
for V ref

## How use jumpers for 3V3 MCU’s (Due etc.)

Jumper for 3V3 IN
3V3 from buck power supply

Jumper for PS2 put on 3V3

No regulator req. here. Use 3V3 PS2 only !

Populate here 3V3 regulator only

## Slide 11

https://www.youtube.com/watch?v=E8GqHvOK4DI&t=646s

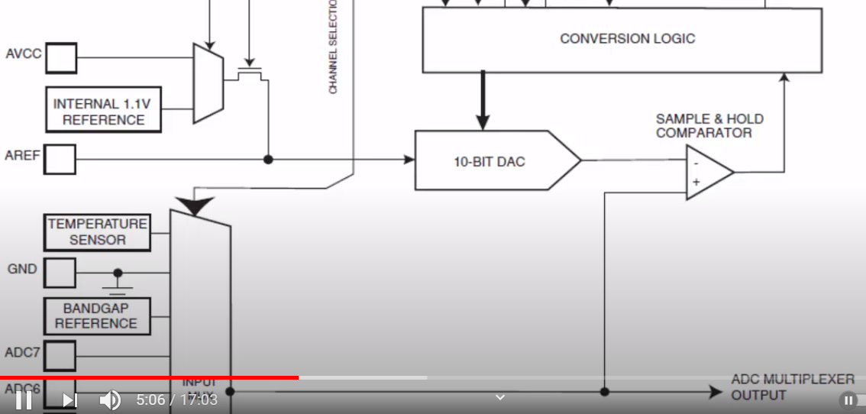
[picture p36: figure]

## Vref: setup external reference voltage for accurate measurment

5V from “5V” pin of the MCU

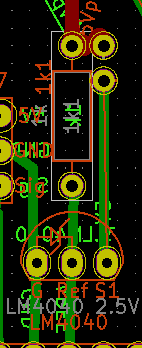
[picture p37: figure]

Bypass jumper to make a separate small PCB for Vref (ferrite signal susp etc.)

GND & 5V for Vref PCB
Signal out on Ref pin

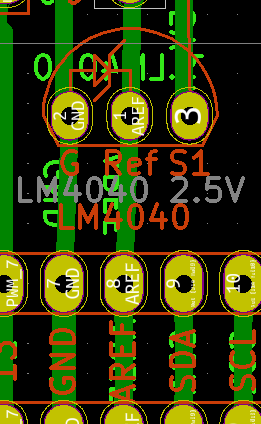
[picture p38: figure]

## V ref mini PCB for improvement

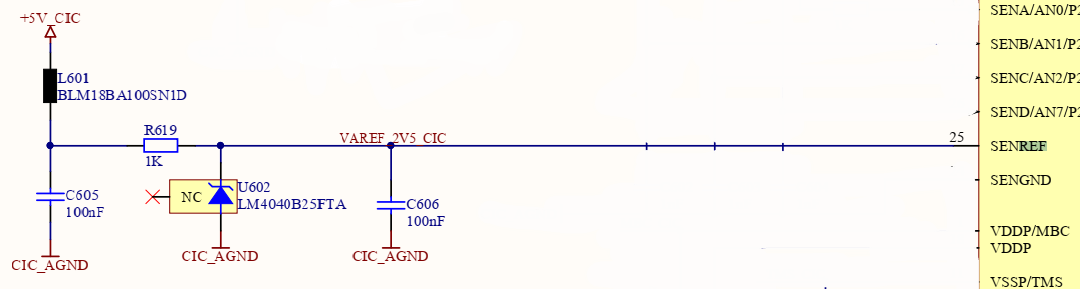
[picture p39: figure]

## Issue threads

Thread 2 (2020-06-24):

Design concept is required.

steger123, 2020-06-24:
Make several conceptual designs, variants for better performance.
For example:
- How the body/chassis the lawnmower looks like?
- How many wheels?
- How many are driven?
- What shall be the shape of the wheel?

steger123, 2020-07-06:
Here You can find a concept for the wheel & transmission:
https://www.tinkercad.com/things/gl9X4MgdXh8-terrific-uusam-densor/edit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

Fell free to improve or suggest other versions.

steger123, 2020-07-06:
The concept for housing:
https://www.tinkercad.com/things/dLuj68VaVWj-housing/edit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

Feel free to improve or suggest other versions.

steger123, 2021-05-05:
Done.

Closed 2021-05-05.

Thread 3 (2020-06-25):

Design the parts

steger123, 2020-06-25:
The body started in Fusion 360.
https://github.com/steger123/Lawn-mower-robot/tree/master/Designs/01_Body

steger123, 2021-05-05:
Your mechanical design lawn mower or other small size rover is up to Your imagination. Only restriction: the shield have 2 outputs /controller signals with encoders for 2 motors.

Closed 2021-05-05.

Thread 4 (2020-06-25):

Which kind of motor will be okay ?

steger123, 2020-06-25:
I would like to have collaborators for an open source project: Lawn Mower Robot (LMR)
Shall be less in weight, but if not HUB motor used, then transmission line getting complicated.

steger123, 2021-05-05:
DC or BLDC can be used as with proper motor controllers. The custom shield just have the power output.

Closed 2021-05-05.

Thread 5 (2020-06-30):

Polyline not dragged on the map in JS Leaflet

steger123, 2020-06-30:
New markers can be placed on the map using the "Route" button, but only the marker is draggable. The **green** line remain in the old position.
Find full working code here:
https://github.com/steger123/Lawn-mower-robot/tree/master/codes/JavaScript/PolyLine
**For suspected issue location in the code searc for "*".**

steger123, 2020-06-30:
Problem solved here:
https://stackoverflow.com/questions/62650814/leaflet-how-to-match-marker-and-polyline-on-drag-and-drop-new-markers-and-lin/62651749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
Credit goes to: **Falke Design**. Thank You very much :-) !
https://stackoverflow.com/users/8283938/falke-design

Closed 2020-06-30.

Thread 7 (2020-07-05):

Any other suggestions warmly welcomed here :-)

steger123, 2020-07-05:
You can address here any other suggestions. Thank You!

s1risaac, 2020-07-05:
What kind of hardware do you plan to use?
A arduino driven robot or rasperry pi with ROS, or what are your ideas at the moment?

steger123, 2020-07-05:
In case of application there can be two scenarios: cut the grass on the backyard or cut the grass on the field.
I would say the on the backyard is easier, because of the range between the robot and operator is short and WiFi/Bluetooth are available.
On the field is different, because the distance bigger (a couple of hundred meters) and no WiFi.
The base computer can run on JavaScript. This will specify the waypoints and send them to the robot via GSM.
(For this, we need precision GPS navigation on the robot as well.)
The robot will connect the waypoints in an autonomous way (vision recognition/obstacle avoidance) reporting via GSM to the base.
So I'm planning to use on the robot Jetson Nano (CPU+ NVIDIA GPU). It is a bigger version of Raspberry Pi (CPU and weak GPU)
The software on the Jetson Nano is Python.

What are Your strengths? Software or hardware or both?

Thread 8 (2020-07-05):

GPS/GNSS/INS receiver navigation system required

steger123, 2020-07-05:
What would be the best for 10 cm accuracy ?

steger123, 2021-05-05:
**Use this GNSS chips:**
BASE: U-Blox ZED-F9P
ROVER: U-Blox ZED-F9R (due to the integrated IMU/electronic compass. Required for heading. Chip's accuracy: 0.2 deg)

**Sparkfun:**
BASE: https://www.sparkfun.com/products/16481
ROVER: https://www.sparkfun.com/products/16344

**or Ardusimple:**
BASE: https://www.ardusimple.com/product/simplertk2blite/
ROVER: https://www.ardusimple.com/product/simplertk2b-f9r-v3

or
BASE: https://www.gnss.store/gnss-gps-modules/99-ublox-zed-f9p-rtk-gnss-receiver-board-with-sma-base-or-rover.html
ROVER: https://www.gnss.store/gnss-gps-modules/134-ublox-zed-f9r-elt0117.html

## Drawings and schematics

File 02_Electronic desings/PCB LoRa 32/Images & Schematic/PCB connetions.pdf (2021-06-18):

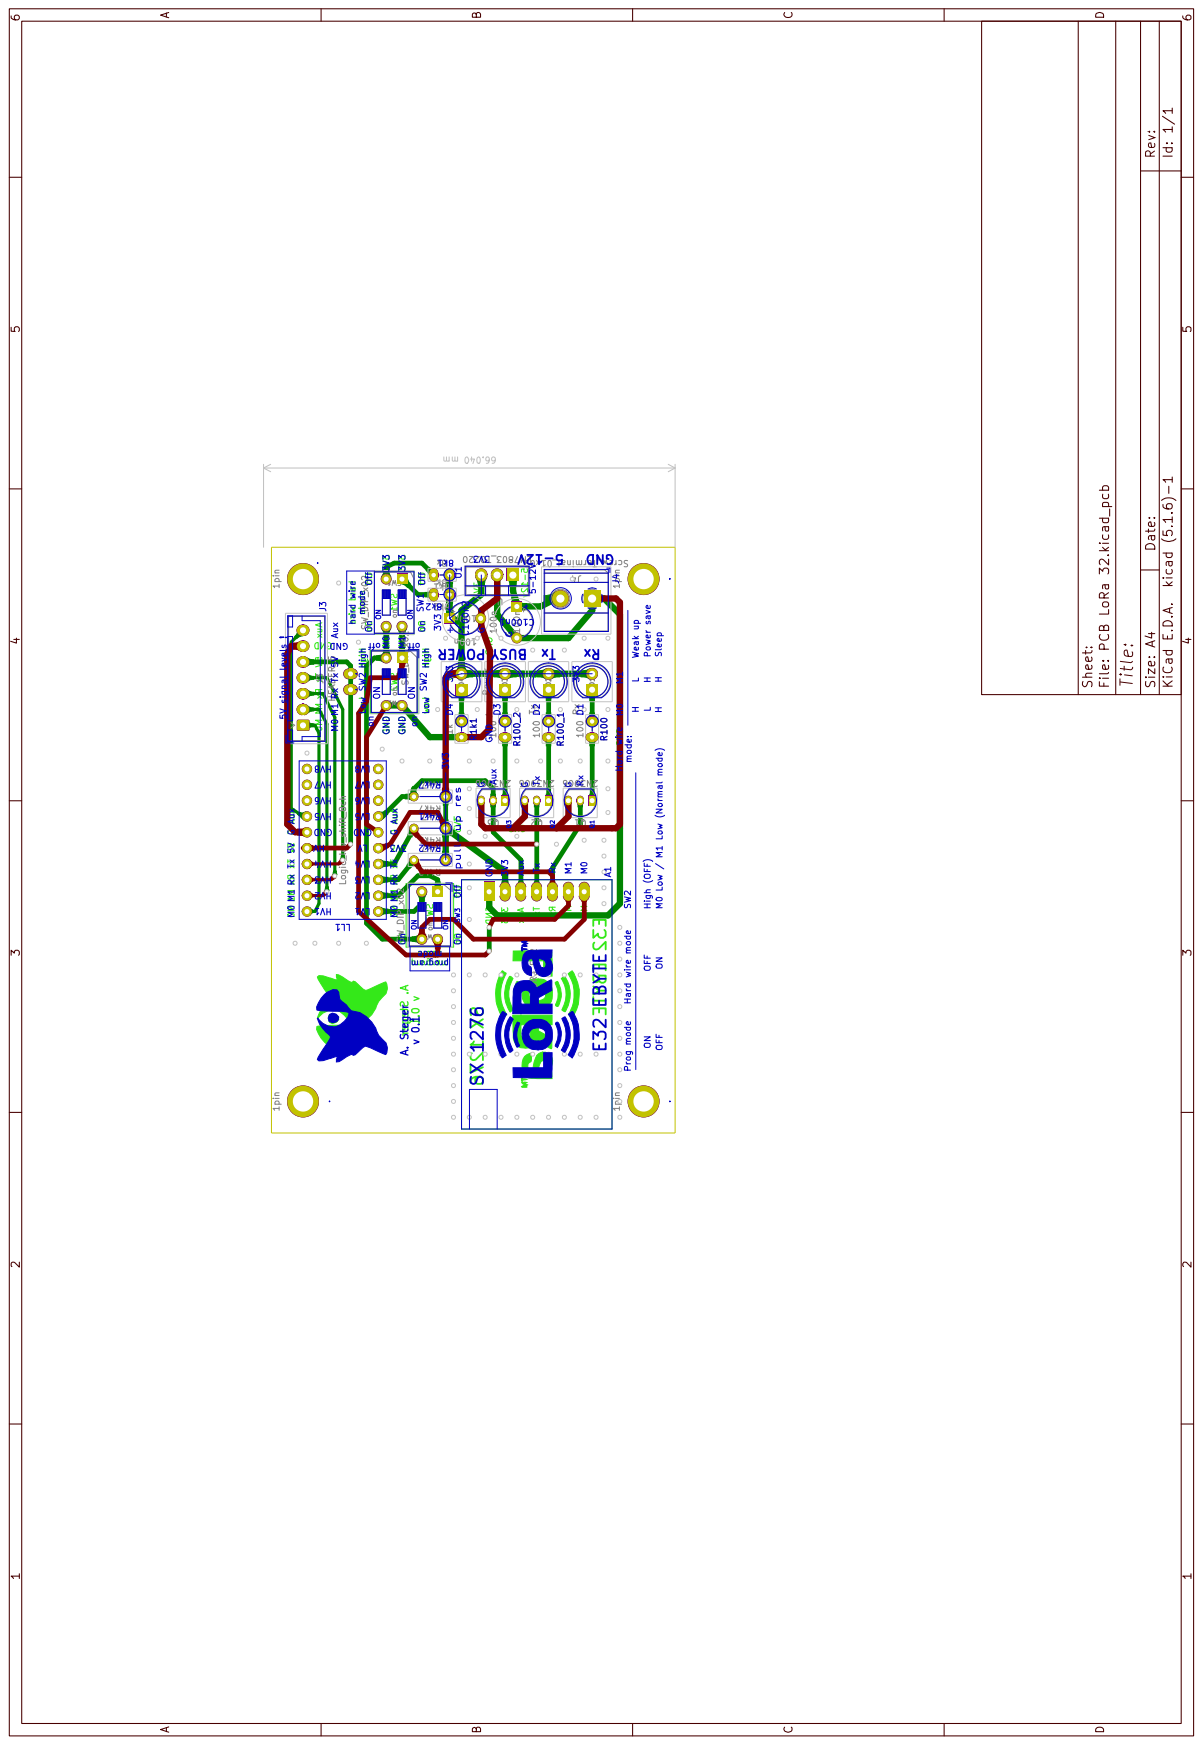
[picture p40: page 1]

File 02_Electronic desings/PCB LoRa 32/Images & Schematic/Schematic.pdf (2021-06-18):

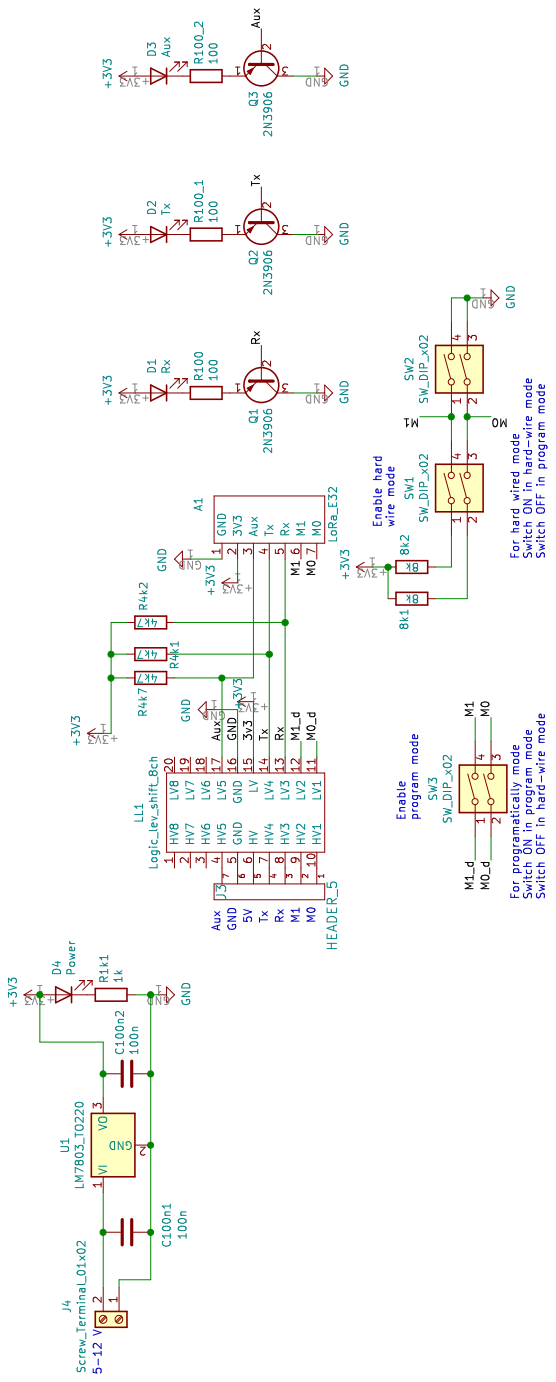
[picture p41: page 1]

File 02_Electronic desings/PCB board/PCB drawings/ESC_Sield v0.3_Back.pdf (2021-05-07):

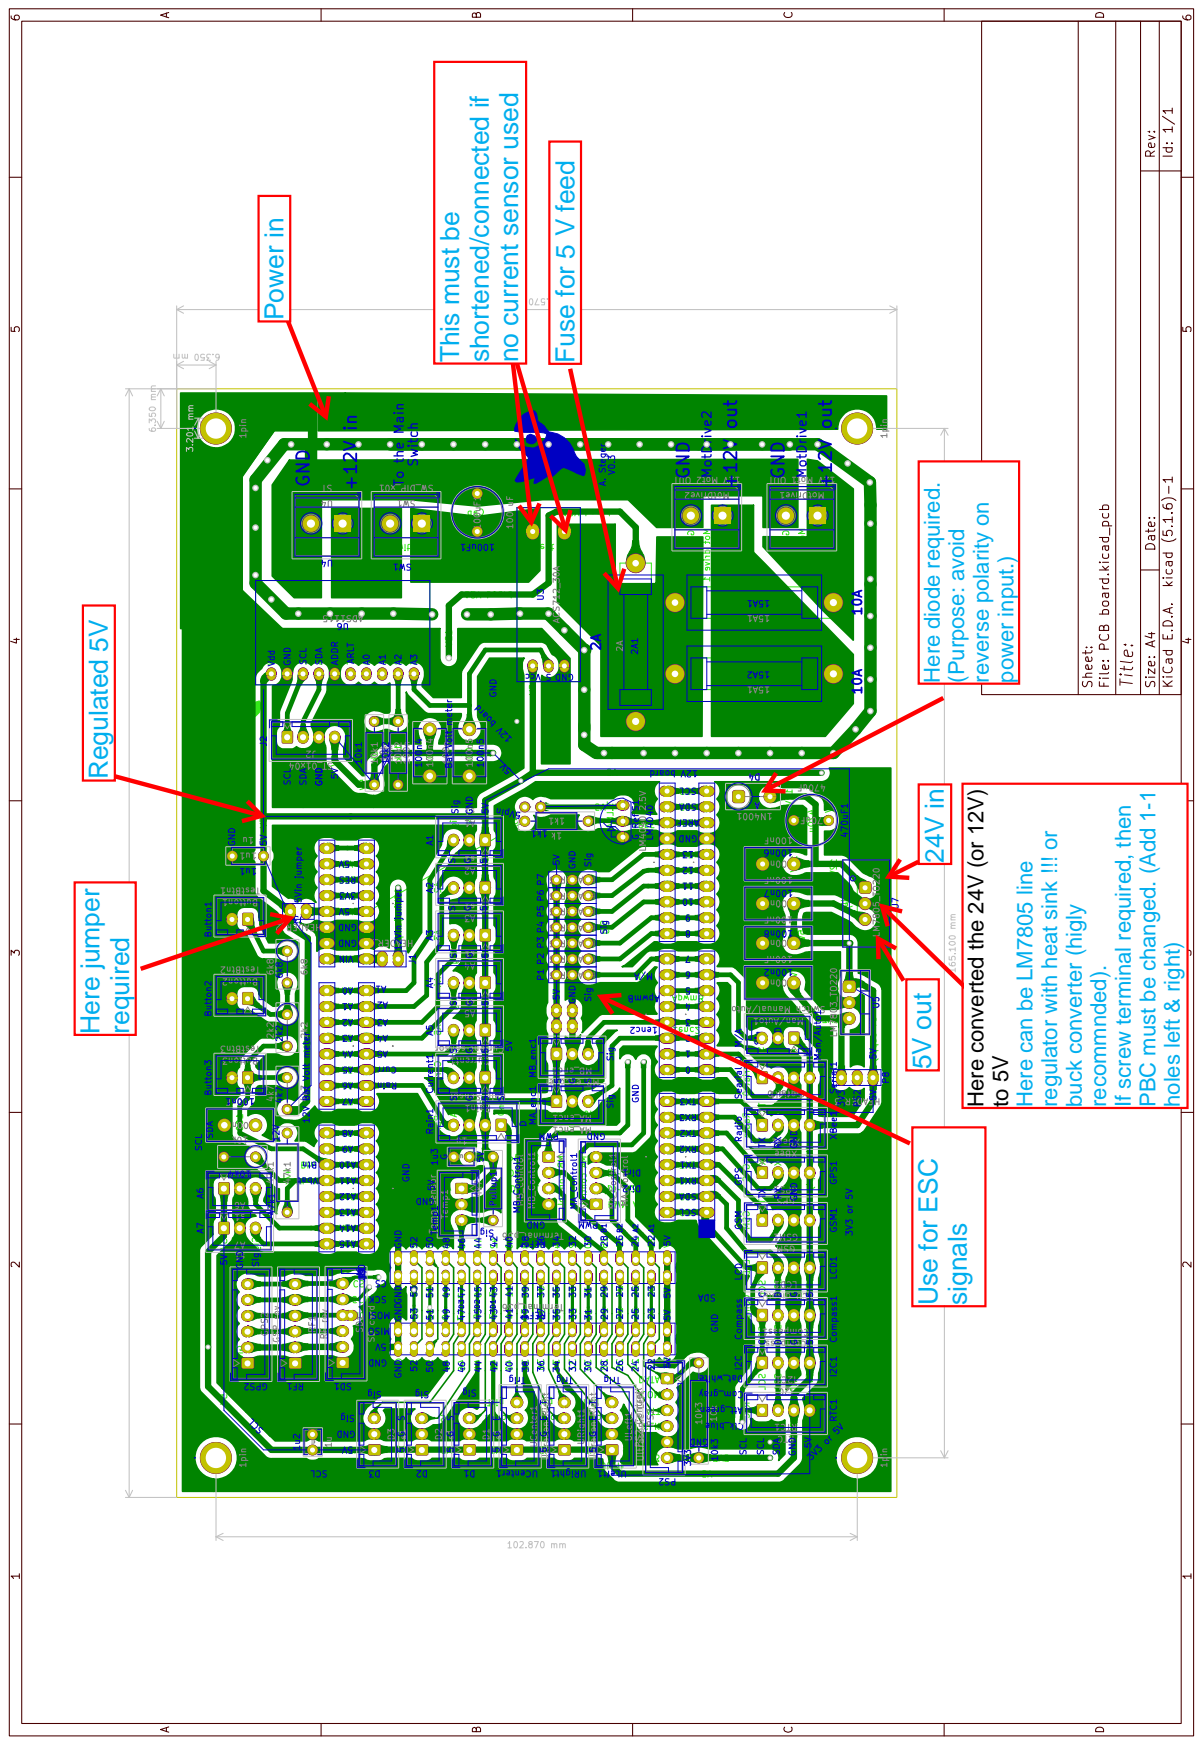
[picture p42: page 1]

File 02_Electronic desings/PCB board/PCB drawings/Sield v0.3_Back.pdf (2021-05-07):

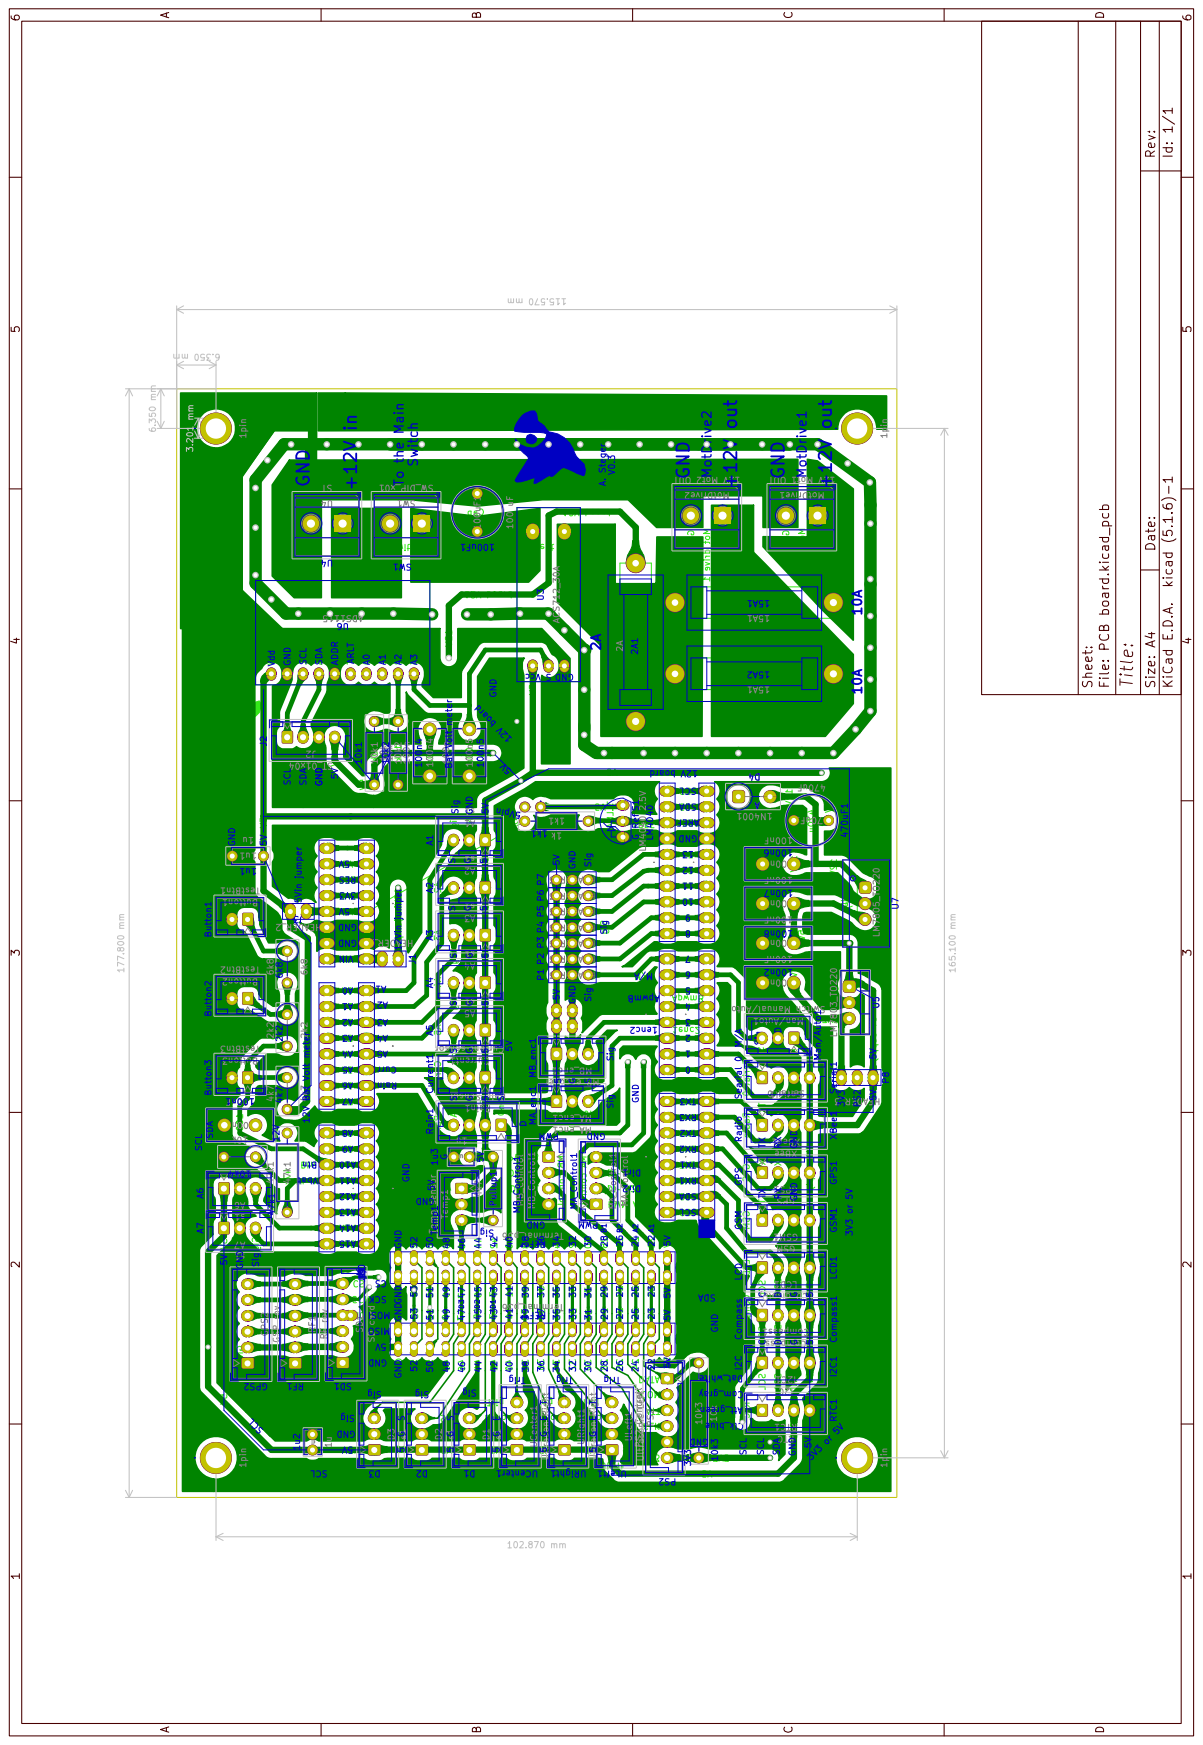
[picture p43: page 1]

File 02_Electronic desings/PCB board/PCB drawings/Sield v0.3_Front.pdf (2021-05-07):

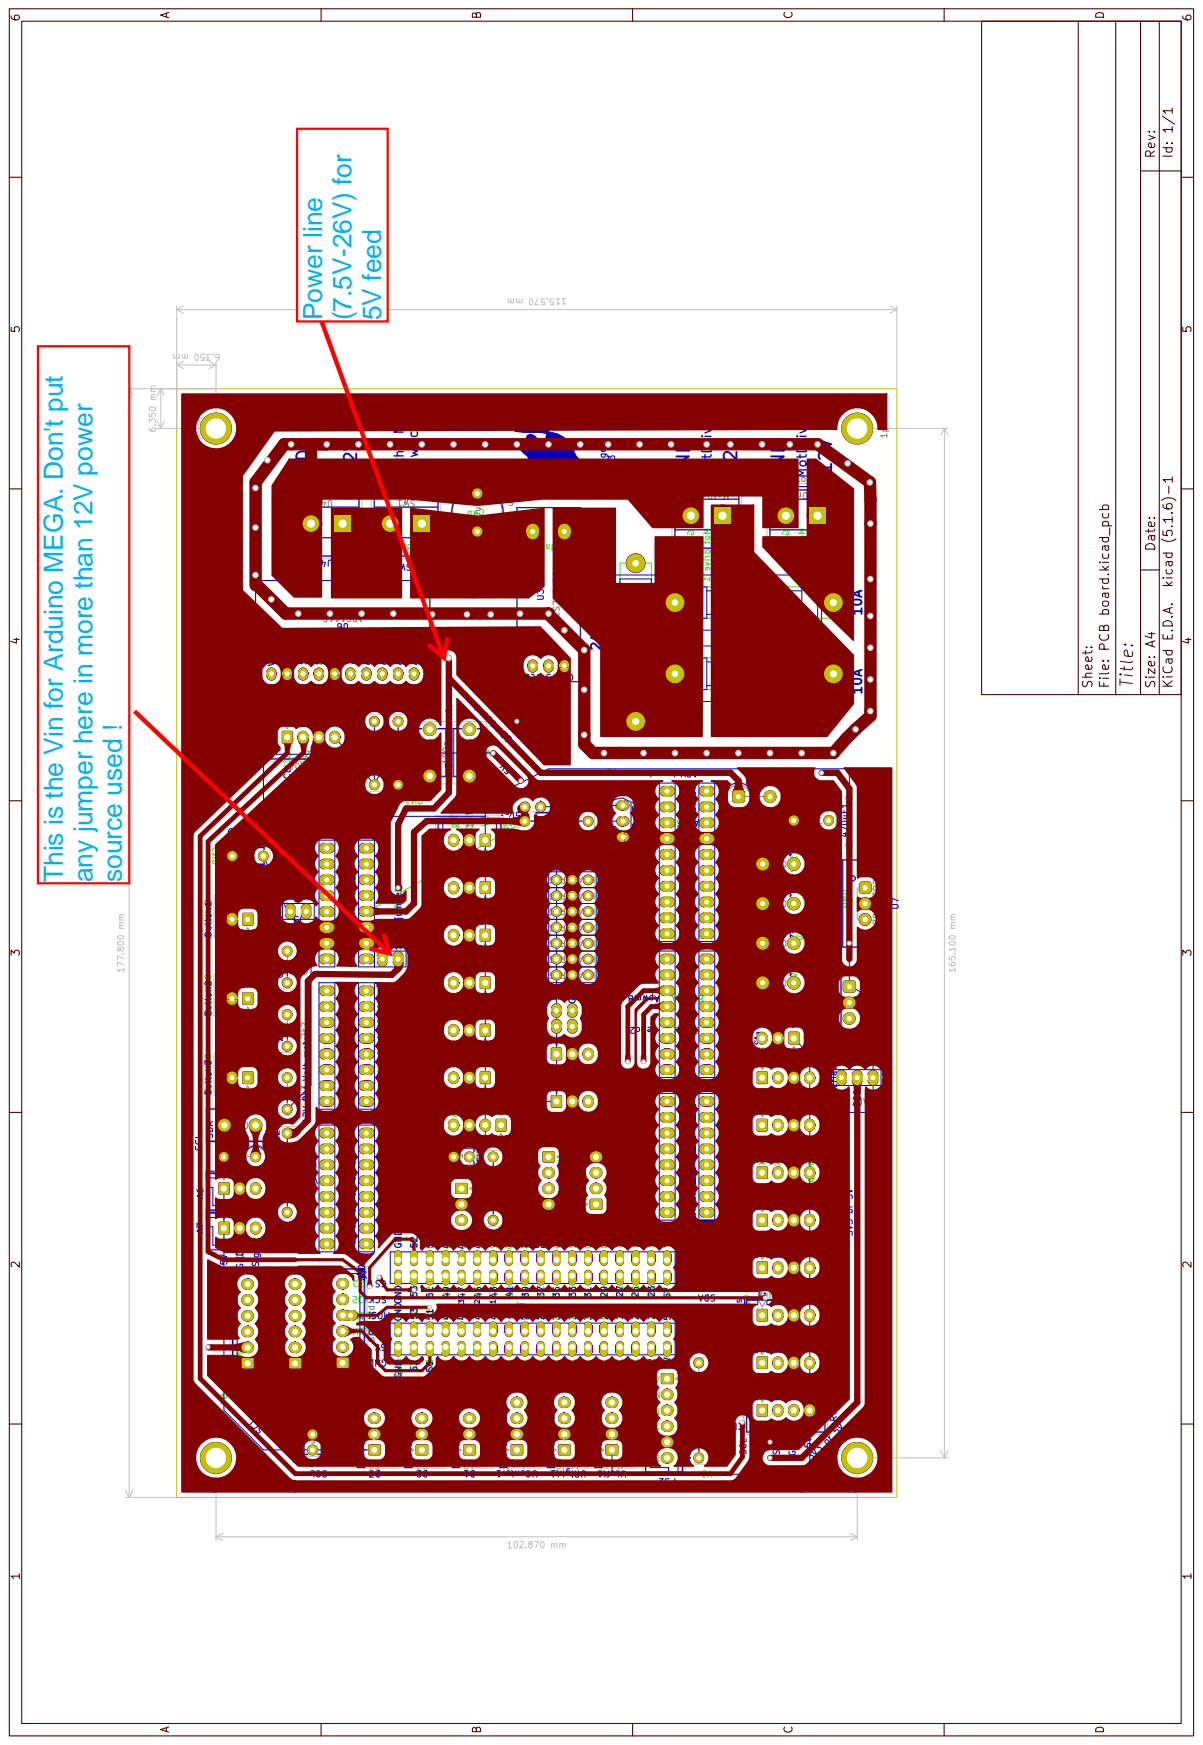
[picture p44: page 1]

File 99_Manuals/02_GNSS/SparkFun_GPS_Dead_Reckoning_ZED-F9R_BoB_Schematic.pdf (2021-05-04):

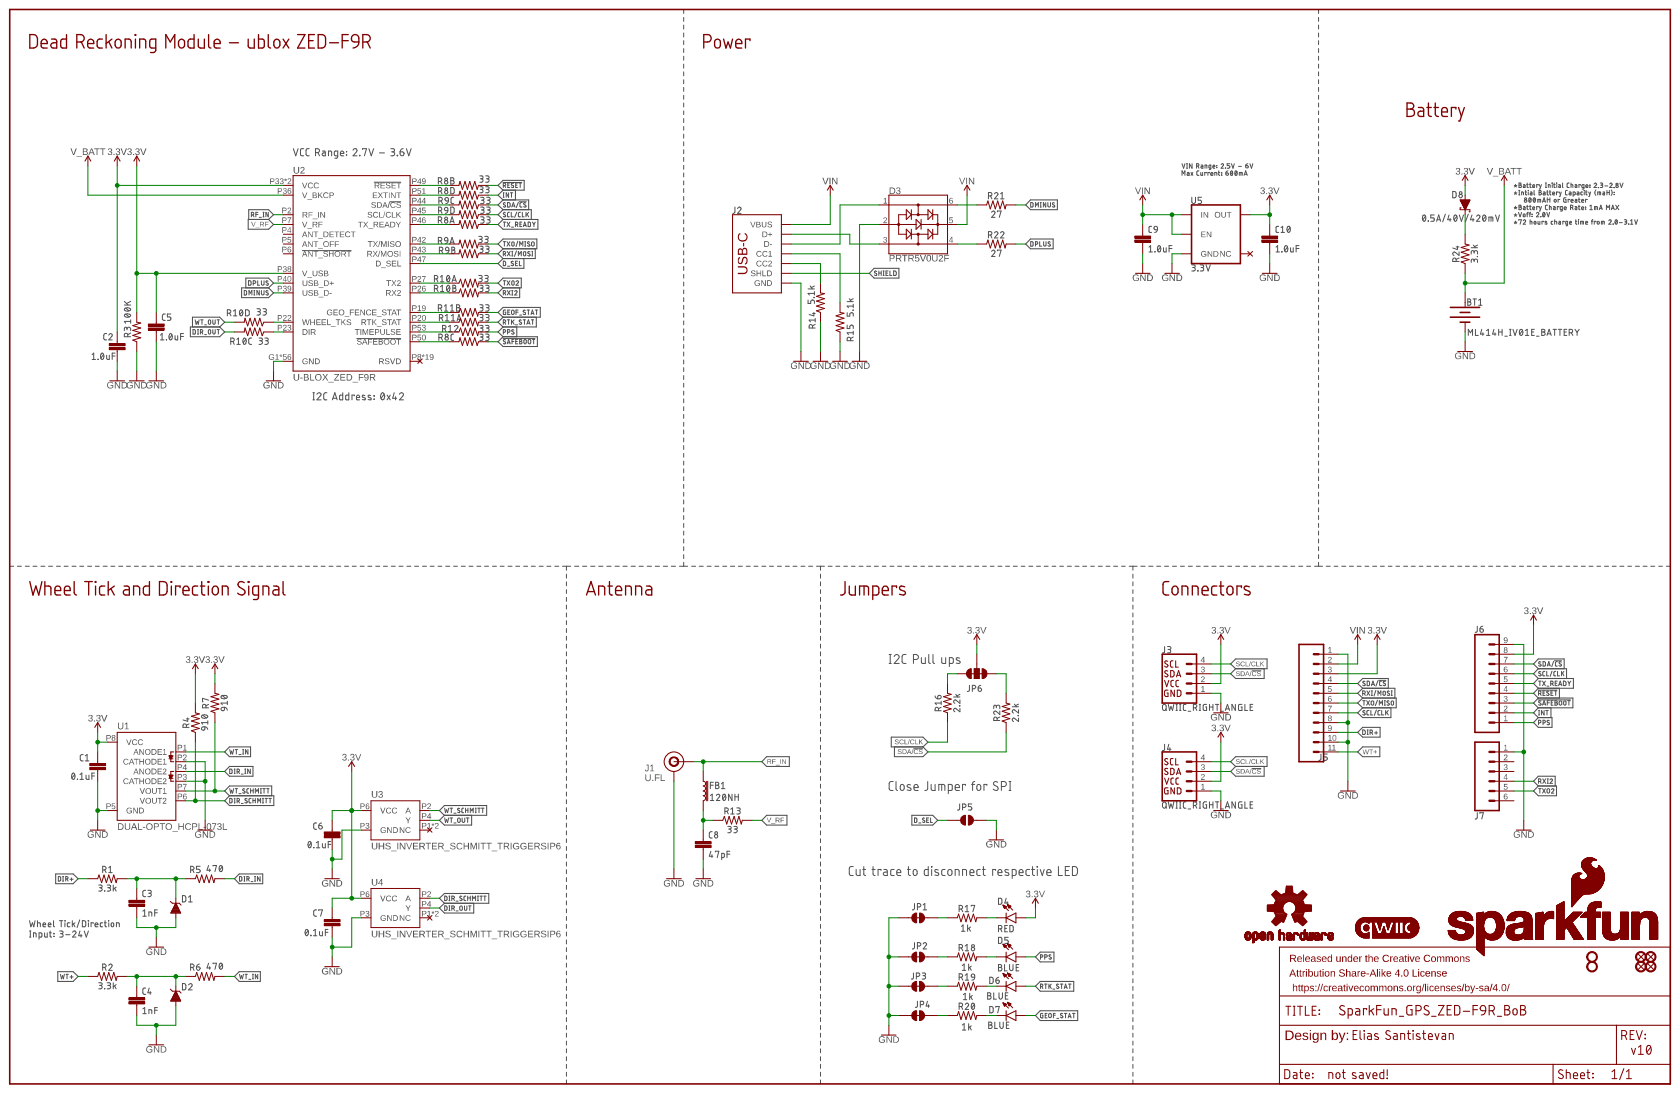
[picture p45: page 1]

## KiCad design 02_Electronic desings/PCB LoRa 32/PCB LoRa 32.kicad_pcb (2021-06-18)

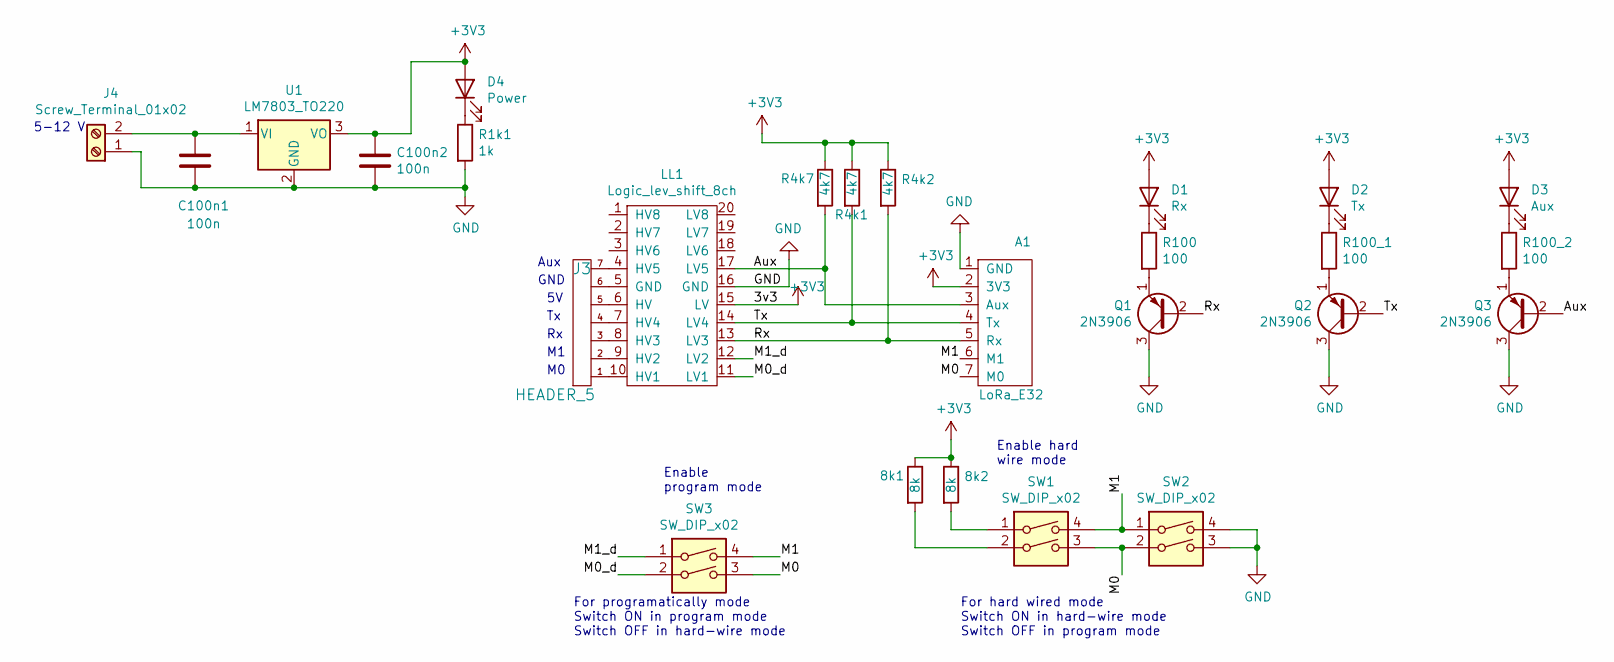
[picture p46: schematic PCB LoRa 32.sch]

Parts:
8k1, 8k2: 8k; R_Axial_DIN0204_L3.6mm_D1.6mm_P2.54mm_Vertical
A1: LoRa_E32
C100n1, C100n2: 100n; CP_Radial_Tantal_D5.0mm_P5.00mm
D1: Rx; LED_D5.0mm
D2: Tx; LED_D5.0mm
D3: Aux; LED_D5.0mm
D4: Power; LED_D5.0mm
J3: HEADER_5; JST_XH_B7B-XH-A_1x07_P2.50mm_Vertical
J4: Screw_Terminal_01x02; TerminalBlock_Phoenix_MKDS-1,5-2-5.08_1x02_P5.08mm_Horizont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
LL1: Logic_lev_shift_8ch
Q1, Q2, Q3: 2N3906; TO-92_Inline
R1k1: 1k; R_Axial_DIN0204_L3.6mm_D1.6mm_P2.54mm_Vertical
R4k1, R4k2, R4k7: 4k7; R_Axial_DIN0204_L3.6mm_D1.6mm_P5.08mm_Vertical
R100, R100_1, R100_2: 100; R_Axial_DIN0204_L3.6mm_D1.6mm_P2.54mm_Vertical
SW1, SW2, SW3: SW_DIP_x02; SW_DIP_SPSTx02_Slide_9.78x7.26mm_W7.62mm_P2.54mm
U1: LM7803_TO220; TO-220-3_Vertical

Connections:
+3V3: 8k1.1, 8k2.1, A1.2 (3V3), C100n2.1, D1.2 (A), D2.2 (A), D3.2 (A), D4.2 (A), LL1.15 (LV), R4k1.1, R4k2.1, R4k7.1, U1.3 (VO)
/Aux: A1.3 (Aux), LL1.17 (LV5), Q3.2 (B), R4k7.2
/M0: A1.7 (M0), SW1.3, SW2.2, SW3.3
/M0_d: LL1.11 (LV1), SW3.2
/M1: A1.6 (M1), SW1.4, SW2.1, SW3.4
/M1_d: LL1.12 (LV2), SW3.1
/Rx: A1.5 (Rx), LL1.13 (LV3), Q1.2 (B), R4k2.2
/Tx: A1.4 (Tx), LL1.14 (LV4), Q2.2 (B), R4k1.2
GND: A1.1 (GND), C100n1.2, C100n2.2, J4.1, LL1.16 (GND), Q1.3 (C), Q2.3 (C), Q3.3 (C), R1k1.2, SW2.3, SW2.4, U1.2 (GND)
unnamed: 8k1.2, SW1.2
unnamed: 8k2.2, SW1.1
unnamed: C100n1.1, J4.2, U1.1 (VI)
unnamed: D1.1 (K), R100.1
unnamed: D2.1 (K), R100_1.1
unnamed: D3.1 (K), R100_2.1
unnamed: D4.1 (K), R1k1.1
unnamed: J3.1, LL1.10 (HV1)
unnamed: J3.2, LL1.9 (HV2)
unnamed: J3.3, LL1.8 (HV3)
unnamed: J3.4, LL1.7 (HV4)
unnamed: J3.5, LL1.6 (HV)
unnamed: J3.6, LL1.5 (GND)
unnamed: J3.7, LL1.4 (HV5)
unnamed: Q1.1 (E), R100.2
unnamed: Q2.1 (E), R100_1.2
unnamed: Q3.1 (E), R100_2.2

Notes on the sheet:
5-12 V
For programatically mode Switch ON in program mode Switch OFF in hard-wire mode
For hard wired mode Switch ON in hard-wire mode Switch OFF in program mode
GND
Aux
Enable hard wire mode
Enable program mode

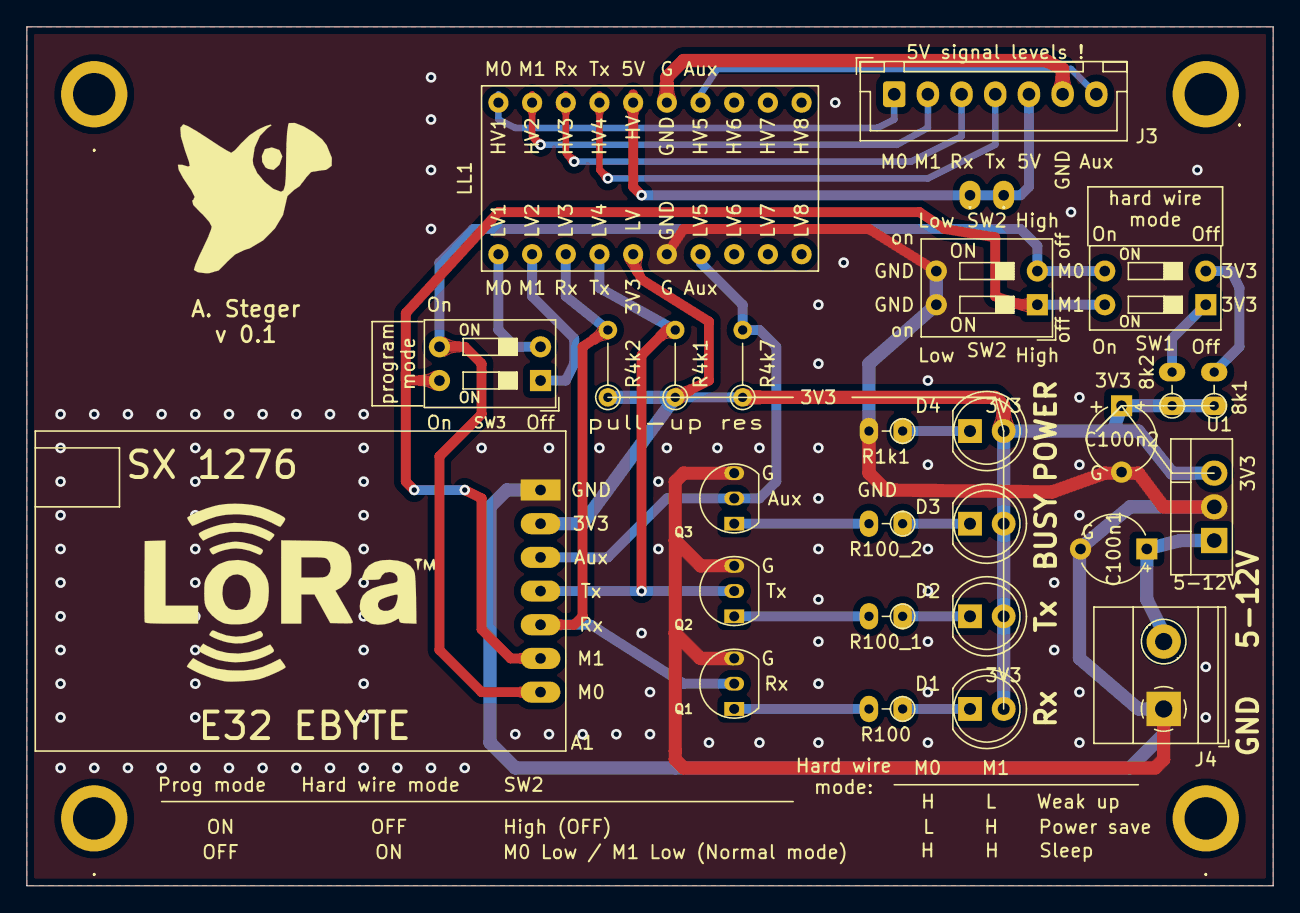
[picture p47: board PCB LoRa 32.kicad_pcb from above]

Board: 2 copper layers, 94.0 x 64.8 mm, 32 parts (0 on the bottom side), 26 nets.

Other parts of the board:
., .#2: .; 1_pin
.#3, .#4, .#5, .#6: 1pin

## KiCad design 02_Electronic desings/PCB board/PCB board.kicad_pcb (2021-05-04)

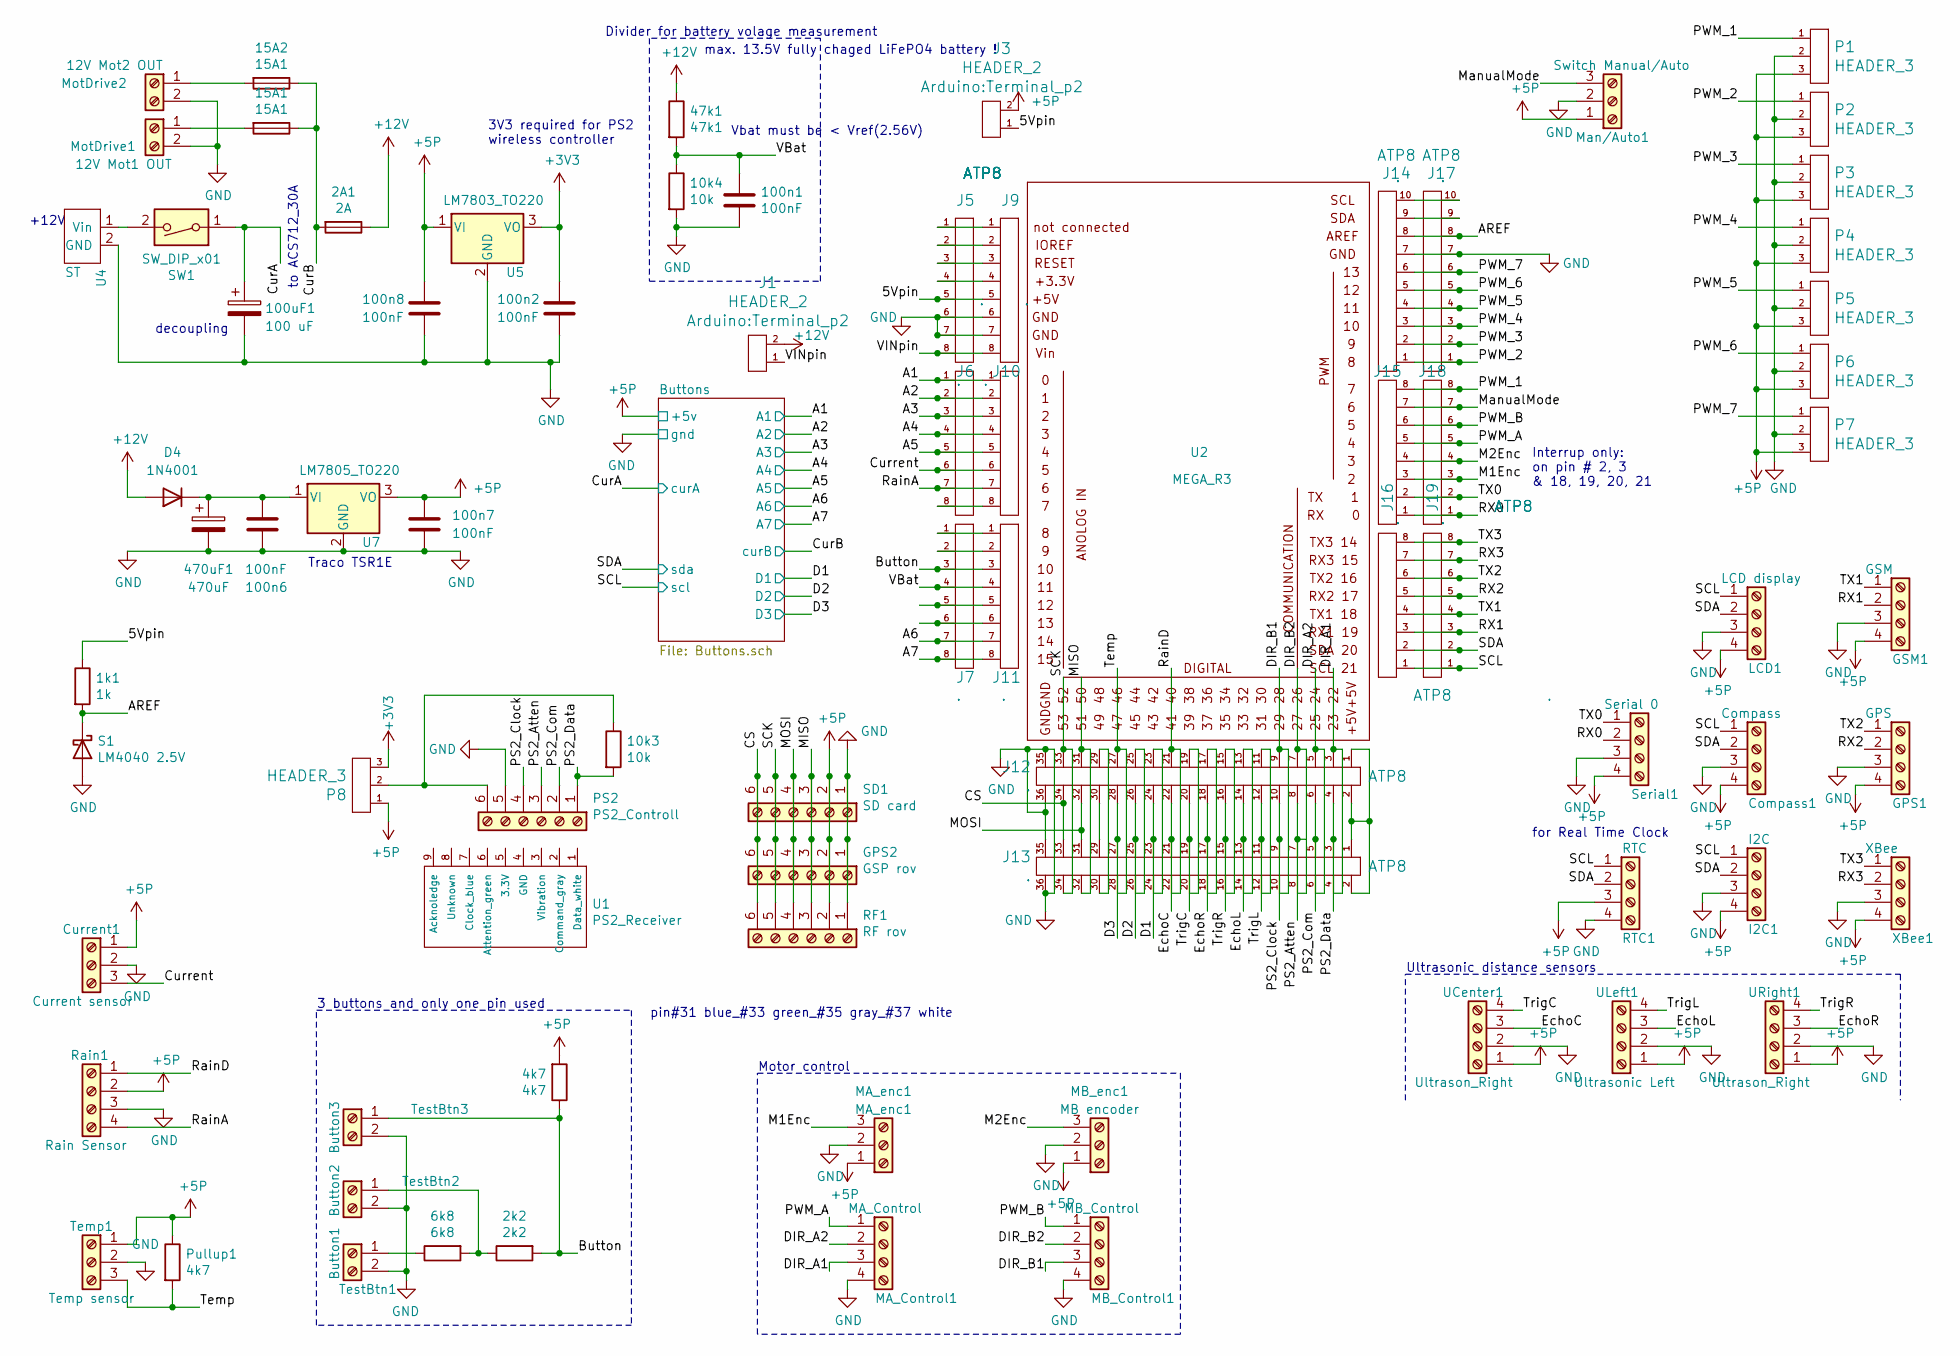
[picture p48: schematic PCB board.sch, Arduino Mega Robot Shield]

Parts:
1k1: 1k; R_Axial_DIN0207_L6.3mm_D2.5mm_P10.16mm_Horizontal
2A1: 2A; Fuse
2k2: 2k2; R_Axial_DIN0309_L9.0mm_D3.2mm_P5.08mm_Vertical
4k7: 4k7; R_Axial_DIN0309_L9.0mm_D3.2mm_P5.08mm_Vertical
6k8: 6k8; R_Axial_DIN0309_L9.0mm_D3.2mm_P5.08mm_Vertical
10k3: 10k; R_Axial_DIN0207_L6.3mm_D2.5mm_P10.16mm_Horizontal
10k4: 10k; R_Axial_DIN0309_L9.0mm_D3.2mm_P5.08mm_Vertical
15A1, 15A2: 15A1; Fuse
47k1: 47k1; R_Axial_DIN0309_L9.0mm_D3.2mm_P12.70mm_Horizontal
100n1, 100n2, 100n6, 100n7, 100n8: 100nF; C_Disc_D10.5mm_W5.0mm_P5.00mm
100uF1: 100 uF; C_Radial_D8.0mm_H7.0mm_P3.50mm
470uF1: 470uF; C_Radial_D8.0mm_H7.0mm_P3.50mm
Button1: TestBtn1; JST_XH_B2B-XH-A_1x02_P2.50mm_Vertical
Button2: TestBtn2; JST_XH_B2B-XH-A_1x02_P2.50mm_Vertical
Button3: TestBtn3; JST_XH_B2B-XH-A_1x02_P2.50mm_Vertical
Compass1: Compass; JST_XH_B4B-XH-A_1x04_P2.50mm_Vertical
Current1: Current sensor; JST_XH_B3B-XH-A_1x03_P2.50mm_Vertical
D4: 1N4001; D_5W_P5.08mm_Vertical_AnodeUp
GPS1: GPS; JST_XH_B4B-XH-A_1x04_P2.50mm_Vertical
GPS2: GSP rov; JST_XH_B6B-XH-A_1x06_P2.50mm_Vertical
GSM1: GSM; JST_XH_B4B-XH-A_1x04_P2.50mm_Vertical
I2C1: I2C; JST_XH_B4B-XH-A_1x04_P2.50mm_Vertical
J1, J3: HEADER_2; Terminal_p2
J5, J6, J7, J9, J10, J11, J12, J13, J14, J15, J17, J18, J19: .; ATP8
J16: .
LCD1: LCD display; JST_XH_B4B-XH-A_1x04_P2.50mm_Vertical
MA_Control1: MA_Control; JST_XH_B4B-XH-A_1x04_P2.50mm_Vertical
MA_enc1: MA_enc1; JST_XH_B3B-XH-A_1x03_P2.50mm_Vertical
MB_Control1: MB_Control; JST_XH_B4B-XH-A_1x04_P2.50mm_Vertical
MB_enc1: MB encoder; JST_XH_B3B-XH-A_1x03_P2.50mm_Vertical
Man/Auto1: Switch Manual/Auto; JST_XH_B3B-XH-A_1x03_P2.50mm_Vertical
MotDrive1: 12V Mot1 OUT; TerminalBlock_Phoenix_MKDS-1,5-2-5.08_1x02_P5.08mm_Horizont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
MotDrive2: 12V Mot2 OUT; TerminalBlock_Phoenix_MKDS-1,5-2-5.08_1x02_P5.08mm_Horizont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
P1, P2, P3, P4, P5, P6, P7: HEADER_3; Terminal_p3_sp
P8: HEADER_3; Terminal_p3
PS2: PS2_Controll; JST_XH_B6B-XH-A_1x06_P2.50mm_Vertical
Pullup1: 4k7; R_Axial_DIN0207_L6.3mm_D2.5mm_P10.16mm_Horizontal
RF1: RF rov; JST_XH_B6B-XH-A_1x06_P2.50mm_Vertical
RTC1: RTC; JST_XH_B4B-XH-A_1x04_P2.50mm_Vertical
Rain1: Rain Sensor; JST_XH_B4B-XH-A_1x04_P2.50mm_Vertical
S1: LM4040 2.5V; TO-92
SD1: SD card; JST_XH_B6B-XH-A_1x06_P2.50mm_Vertical
SW1: SW_DIP_x01; TerminalBlock_Phoenix_MKDS-1,5-2-5.08_1x02_P5.08mm_Horizont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
Serial1: Serial 0; JST_XH_B4B-XH-A_1x04_P2.50mm_Vertical
Temp1: Temp sensor; JST_XH_B3B-XH-A_1x03_P2.50mm_Vertical
U1: PS2_Receiver
U2: MEGA_R3
U4: ST; TerminalBlock_Phoenix_MKDS-1,5-2-5.08_1x02_P5.08mm_Horizont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
U5: LM7803_TO220; TO-220-3_Vertical
U7: LM7805_TO220; Traco_TSR2
UCenter1: Ultrason_Right; JST_XH_B4B-XH-A_1x04_P2.50mm_Vertical
ULeft1: Ultrasonic Left; JST_XH_B4B-XH-A_1x04_P2.50mm_Vertical
URight1: Ultrason_Right; JST_XH_B4B-XH-A_1x04_P2.50mm_Vertical
XBee1: XBee; JST_XH_B4B-XH-A_1x04_P2.50mm_Vertical

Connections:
+3V3: 100n2.1, P8.3, U5.3 (VO)
+5P: 4k7.2, 100n7.1, 100n8.1, Compass1.4, Current1.1, GPS1.4, GPS2.2, GSM1.4, I2C1.4, J3.2, LCD1.4, MA_enc1.1, MB_enc1.1, Man/Auto1.1, P1.3, P2.3, P3.3, P4.3, P5.3, P6.3, P7.3, P8.1, Pullup1.1, RF1.2, RTC1.3, Rain1.2, SD1.2, Serial1.4, Temp1.1, U5.1 (VI), U7.3 (VO), UCenter1.1, ULeft1.1, URight1.1, XBee1.4; also elsewhere on the board
+12V: 2A1.1, 47k1.1, D4.1 (A), J1.2
/5Vpin: 1k1.1, J3.1, J5.5, J9.5
/A1: J6.1, J10.1; also elsewhere on the board
/A2: J6.2, J10.2; also elsewhere on the board
/A3: J6.3, J10.3; also elsewhere on the board
/A4: J6.4, J10.4; also elsewhere on the board
/A5: J6.5, J10.5; also elsewhere on the board
/A6: J7.7, J11.7; also elsewhere on the board
/A7: J7.8, J11.8; also elsewhere on the board
/AREF: 1k1.2, J14.8, J17.8, S1.1 (K)
/Button: 2k2.2, 4k7.1, Button3.1, J7.3, J11.3
/CS: GPS2.6, J12.34, J13.33, RF1.6, SD1.6
/CurA: 100uF1.1, SW1.1; also elsewhere on the board
/CurB: 2A1.2, 15A1.1, 15A2.1; also elsewhere on the board
/Current: Current1.3, J6.6, J10.6
/DIR_A1: J12.3, J13.4, MA_Control1.3
/DIR_A2: J12.5, J13.6, MA_Control1.2
/DIR_B1: J12.9, J13.10, MB_Control1.3
/DIR_B2: J12.7, J13.8, MB_Control1.2
/EchoC: J12.22, J13.21, UCenter1.3
/EchoL: J12.14, J13.13, ULeft1.3
/EchoR: J12.18, J13.17, URight1.3
/M1Enc: J15.3, J18.3, MA_enc1.3
/M2Enc: J15.4, J18.4, MB_enc1.3
/MISO: GPS2.3, J12.31, J13.32, RF1.3, SD1.3
/MOSI: GPS2.4, J12.32, J13.31, RF1.4, SD1.4
/ManualMode: J15.7, J18.7, Man/Auto1.3
/PS2_Atten: J12.8, J13.7, PS2.3
/PS2_Clock: J12.10, J13.9, PS2.4
/PS2_Com: J12.6, J13.5, PS2.2
/PS2_Data: 10k3.2, J12.4, J13.3, PS2.1
/PWM_1: J15.8, J18.8, P1.1
/PWM_2: J14.1, J17.1, P2.1
/PWM_3: J14.2, J17.2, P3.1
/PWM_4: J14.3, J17.3, P4.1
/PWM_5: J14.4, J17.4, P5.1
/PWM_6: J14.5, J17.5, P6.1
/PWM_7: J14.6, J17.6, P7.1
/PWM_A: J15.5, J18.5, MA_Control1.1
/PWM_B: J15.6, J18.6, MB_Control1.1
/RX0: J15.1, J18.1, Serial1.2
/RX1: GSM1.2, J16.3, J19.3
/RX2: GPS1.2, J16.5, J19.5
/RX3: J16.7, J19.7, XBee1.2
/RainA: J6.7, J10.7, Rain1.4
/RainD: J12.21, J13.22, Rain1.1
/SCK: GPS2.5, J12.33, J13.34, RF1.5, SD1.5
/SCL: Compass1.1, I2C1.1, J16.1, J19.1, LCD1.1, RTC1.1; also elsewhere on the board
/SDA: Compass1.2, I2C1.2, J16.2, J19.2, LCD1.2, RTC1.2; also elsewhere on the board
/TX0: J15.2, J18.2, Serial1.1
/TX1: GSM1.1, J16.4, J19.4
/TX2: GPS1.1, J16.6, J19.6
/TX3: J16.8, J19.8, XBee1.1
/Temp: J12.27, J13.28, Pullup1.2, Temp1.3
/TrigC: J12.20, J13.19, UCenter1.4
/TrigL: J12.12, J13.11, ULeft1.4
/TrigR: J12.16, J13.15, URight1.4
/VBat: 10k4.1, 47k1.2, 100n1.1, J7.4, J11.4
/VINpin: J1.1, J5.8, J9.8
GND: 10k4.2, 100n1.2, 100n2.2, 100n6.2, 100n7.2, 100n8.2, 100uF1.2, 470uF1.2, Button1.2, Button2.2, Button3.2, Compass1.3, Current1.2, GPS1.3, GPS2.1, GSM1.3, I2C1.3, J5.6, J5.7, J9.6, J9.7, J12.35, J12.36, J13.35, J13.36, J14.7, J17.7, LCD1.3, MA_Control1.4, MA_enc1.2, MB_Control1.4, MB_enc1.2, Man/Auto1.2, MotDrive1.2, MotDrive2.2, P1.2, P2.2, P3.2, P4.2, P5.2, P6.2, P7.2, PS2.5, RF1.1, RTC1.4, Rain1.3, S1.2 (A), SD1.1, Serial1.3, Temp1.2, U4.2 (GND), U5.2 (GND), U7.2 (GND), UCenter1.2, ULeft1.2, URight1.2, XBee1.3; also elsewhere on the board
unnamed: 2k2.1, 6k8.2, Button2.1
unnamed: 6k8.1, Button1.1
unnamed: 10k3.1, P8.2, PS2.6
unnamed: 15A1.2, MotDrive1.1
unnamed: 15A2.2, MotDrive2.1
unnamed: 100n6.1, 470uF1.1, D4.2 (K), U7.1 (VI)
unnamed: J5.1, J9.1
unnamed: J5.2, J9.2
unnamed: J5.3, J9.3
unnamed: J5.4, J9.4
unnamed: J6.8, J10.8
unnamed: J7.1, J11.1
unnamed: J7.2, J11.2
unnamed: J7.5, J11.5
unnamed: J7.6, J11.6
unnamed: J12.1, J12.2, J13.1, J13.2
unnamed: J12.11, J13.12
unnamed: J12.13, J13.14
unnamed: J12.15, J13.16
unnamed: J12.17, J13.18
unnamed: J12.19, J13.20
unnamed: J12.23, J13.24
unnamed: J12.24, J13.23
unnamed: J12.25, J13.26
unnamed: J12.26, J13.25
unnamed: J12.28, J13.27
unnamed: J12.29, J13.30
unnamed: J12.30, J13.29
unnamed: J14.9, J17.9
unnamed: J14.10, J17.10
unnamed: SW1.2, U4.1 (Vin)

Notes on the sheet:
pin#31 blue_#33 green_#35 gray_#37 white
to ACS712_30A
+12V
decoupling
3 buttons and only one pin used
Motor control
Ultrasonic distance sensors
Divider for battery volage measurement
3V3 required for PS2 wireless controller
Traco TSR1E
for Real Time Clock
Vbat must be < Vref(2.56V)
max. 13.5V fully chaged LiFePO4 battery !
Interrup only: on pin # 2, 3 & 18, 19, 20, 21

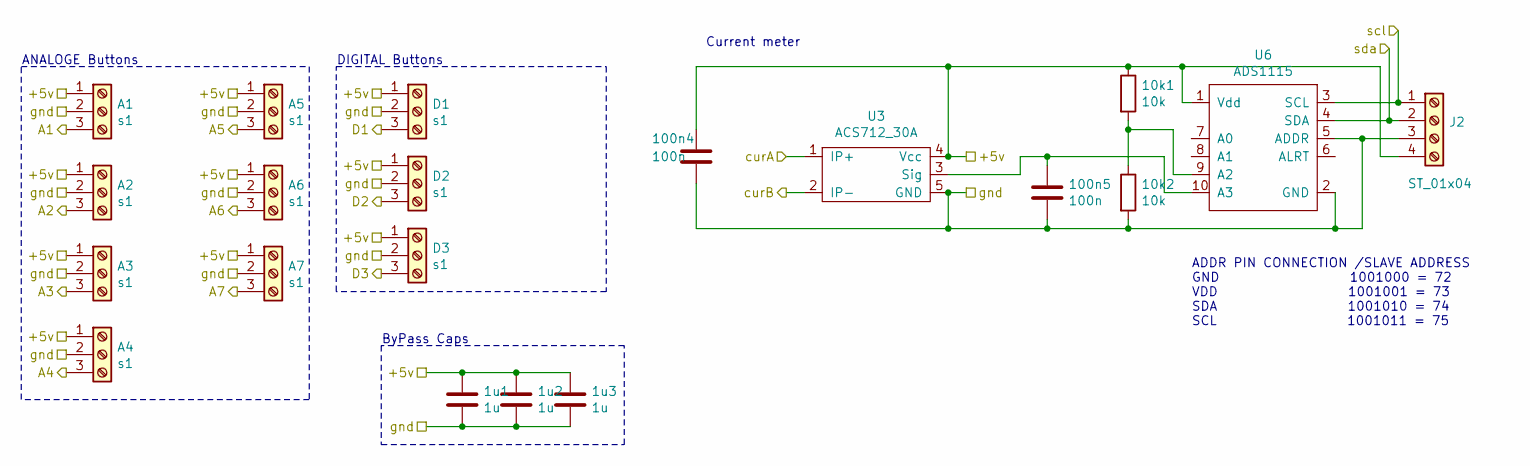
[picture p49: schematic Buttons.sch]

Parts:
1u1: 1u; C_Disc_D5.0mm_W2.5mm_P5.00mm
1u2, 1u3: 1u; C_Disc_D3.8mm_W2.6mm_P2.50mm
10k1, 10k2: 10k; R_Axial_DIN0207_L6.3mm_D2.5mm_P10.16mm_Horizontal
100n4, 100n5: 100n; C_Disc_D7.5mm_W5.0mm_P7.50mm
A1, A2, A3, A4, A5, A6, A7: s1; JST_XH_B3B-XH-A_1x03_P2.50mm_Vertical
D1, D2, D3: s1; JST_XH_B3B-XH-A_1x03_P2.50mm_Vertical
J2: ST_01x04; JST_XH_B4B-XH-A_1x04_P2.50mm_Vertical
U3: ACS712_30A; ASC712
U6: ADS1115

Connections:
+5P: 1u1.1, 1u2.1, 1u3.1, 10k1.1, 100n4.1, A1.1, A2.1, A3.1, A4.1, A5.1, A6.1, A7.1, D1.1, D2.1, D3.1, J2.4, U3.4 (Vcc), U6.1 (Vdd); also elsewhere on the board
/A1: A1.3; also elsewhere on the board
/A2: A2.3; also elsewhere on the board
/A3: A3.3; also elsewhere on the board
/A4: A4.3; also elsewhere on the board
/A5: A5.3; also elsewhere on the board
/A6: A6.3; also elsewhere on the board
/A7: A7.3; also elsewhere on the board
/CurA: U3.1 (IP+); also elsewhere on the board
/CurB: U3.2 (IP-); also elsewhere on the board
/D1: D1.3
/D2: D2.3
/D3: D3.3
/SCL: J2.1, U6.3 (SCL); also elsewhere on the board
/SDA: J2.2, U6.4 (SDA); also elsewhere on the board
GND: 1u1.2, 1u2.2, 1u3.2, 10k2.2, 100n4.2, 100n5.2, A1.2, A2.2, A3.2, A4.2, A5.2, A6.2, A7.2, D1.2, D2.2, D3.2, J2.3, U3.5 (GND), U6.2 (GND), U6.5 (ADDR); also elsewhere on the board
unnamed: 10k1.2, 10k2.1, U6.9 (A2)
unnamed: 100n5.1, U3.3 (Sig), U6.10 (A3)

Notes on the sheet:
ANALOGE Buttons
DIGITAL Buttons
ADDR PIN CONNECTION /SLAVE ADDRESS GND 1001000 = 72 VDD 1001001 = 73 SDA 1001010 = 74 SCL 1001011 = 75
Current meter
ByPass Caps

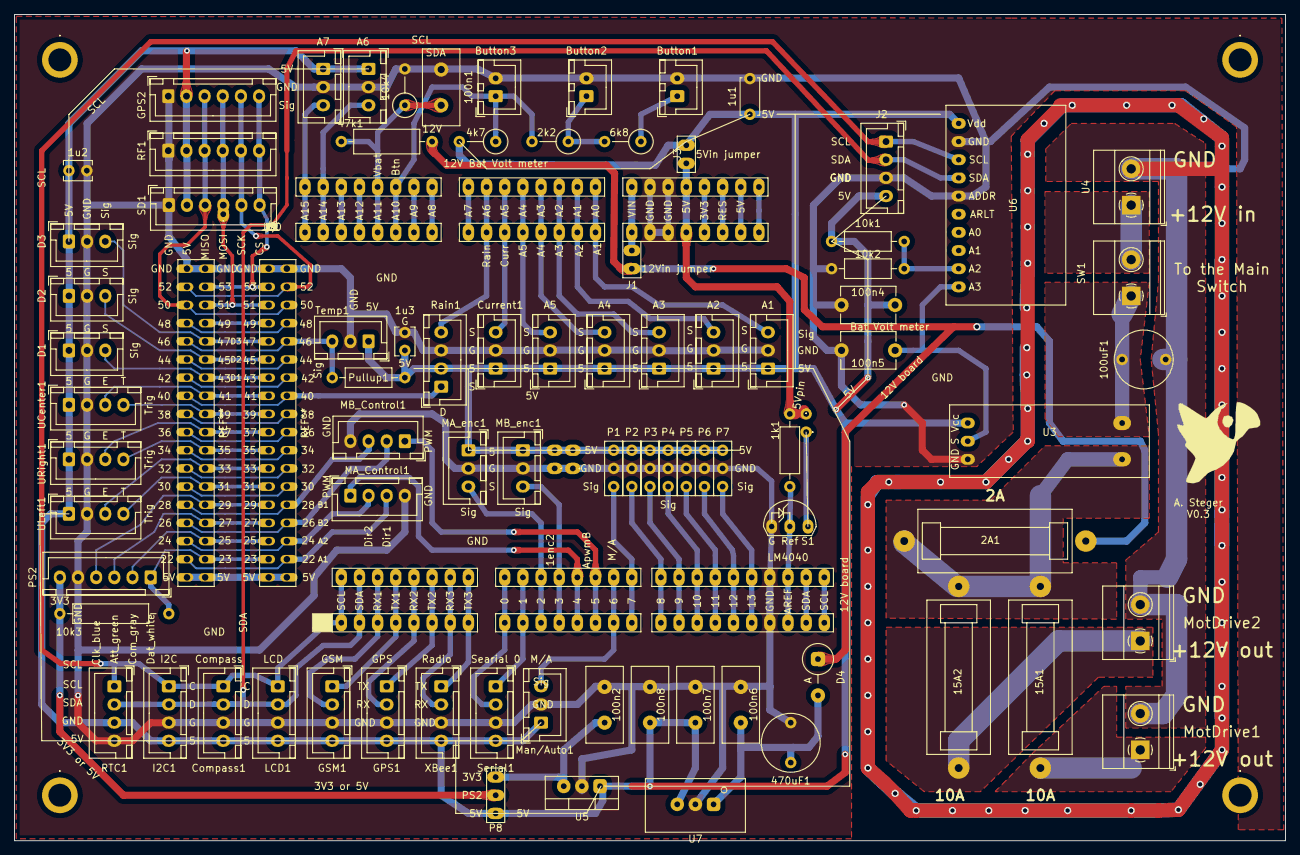
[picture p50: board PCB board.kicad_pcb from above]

Board: 2 copper layers, 177.8 x 115.6 mm, 105 parts (0 on the bottom side), 68 nets.

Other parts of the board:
., .#2, .#3, .#4, .#5, .#6, .#7: .; 1_pin
.#8, .#9, .#10, .#11: 1pin

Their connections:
+5P: .#4.1, .#5.1; also elsewhere on the board

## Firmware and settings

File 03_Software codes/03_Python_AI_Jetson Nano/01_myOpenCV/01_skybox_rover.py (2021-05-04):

# jetbot@jetson-4-3:~/Desktop/pyPro/myOpenCV$ /usr/bin/python3 /home/jetbot/Desktop/pyPro/myOpenCV/edgeLineVideo.py
import cv2
import numpy as np
import time
import serial
#List serial ports:
#$ dmesg | grep tty

usb = 'USB0'
dangWidth = 20  # danger zone width
dangHeight = 50
roiWidth = 80  #total is 2*60=120

cam=cv2.VideoCapture(0)
# used to record the time when we processed last frame 
prev_frame_time = 0
# used to record the time at which we processed current frame 
new_frame_time = 0
font = cv2.FONT_HERSHEY_PLAIN

while True:

    ret, frame =cam.read()
    #roi = cv2.imread('f1.jpg')qq

    # cv2.waitKey(0)
    key = cv2.waitKey(1)
    if key == 27 or key == ord('q'):  #esc
    #if cv2.waitKey(1)==ord('q'):
        break
    if cv2.waitKey(1)==ord('c'):
        cv2.imwrite('/home/jetbot/Desktop/pyPro/myOpenCV/img/captured.jpg', frame)
        print('image captured')

    roi = frame[280:480, (320 - roiWidth):(320 + roiWidth)]  # 640x480
    #roi = frame[280:480, 220:420]   # 640x480
    cv2.imshow('ROI', roi)
    cv2.moveWindow('ROI',0,0)

    hsv = cv2.cvtColor(roi, cv2.COLOR_BGR2HSV)
    hueImg, satImg, valImg = cv2.split(hsv)
    hueMask = cv2.inRange(hueImg, 50,170)  #10,80
    satMask = cv2.inRange(satImg, 70,220)  #100,250 
    valMask = cv2.inRange(valImg, 30,80)  #100,250  
    hueMask = hueMask & satMask & valMask
    cv2.imshow("COMBO_MASK", hueMask)
    cv2.moveWindow('COMBO_MASK',230,0)

#noNoise = cv2.fastNlMeansDenoising(hueMask,250,7,21)
#cv2.imshow("NO_NOISE", noNoise)
#cv2.moveWindow('NO_NOISE',1000,150)

    vertical = np.copy(hueMask)
    rows = vertical.shape[0]
    verticalsize = rows // 9   #influencing the target direction !!!
# Create structure element for extracting vertical lines through morphology operations
    verticalStructure = cv2.getStructuringElement(cv2.MORPH_RECT, (1, verticalsize))
    vertical = cv2.erode(vertical, verticalStructure)
    vertical = cv2.dilate(vertical, verticalStructure)
    cv2.imshow("COMBO_VERTICAL", vertical)
    cv2.moveWindow('COMBO_VERTICAL',400,0)

    contours, hierarhy = cv2.findContours(vertical, cv2.RETR_TREE, cv2.CHAIN_APPROX_SIMPLE)
    roi = cv2.drawContours(roi, contours, -1, (0,0,250), 1)
    cv2.fillPoly(roi, pts =contours, color=(255,0,255))
    cv2.imshow('CONTOUR', roi)
    cv2.moveWindow('CONTOUR',600,0)

#get contur centers
    contours_poly = len(contours)
    center = len(contours)
    radius = len(contours)
#find enclosing polygon which fits around the contures
    rMax = 1
    origo = (100,100)
    for i in range(0,len(contours)):
	    cont = contours[i]
	    approx = cv2.approxPolyDP(cont, 2, True)
	    #(x,y),radius = cv2.minEnclosingCircle(approx)
	    (x,y),radius = cv2.minEnclosingCircle(cont)
	    center = (int(x), int(y))
	    radius = int(radius)
	    frameCircle = cv2.circle(roi, center, radius, (255,0,0), 2)
	    if x>0 and x<640 and y>0 and y<480:  #ROI window for region of interes can be smaller (not the full window)
		    if int(radius) > rMax:
			    rMax = int(radius)
			    origo = center
    # print("rMax & origo: ", rMax, origo)  # rMax or origo can be 0 !
    frameCircle = cv2.line(roi, (roiWidth, 200), (roiWidth, 100), (0, 255, 255), 2)  # heading yellow line
    frameCircle = cv2.line(roi, (roiWidth, 200), origo, (0, 0, 250), 2)  # direction required red line

    # calculate angle:
    x11 = roiWidth  # bottom point for heading
    y11 = 200
    x12 = roiWidth  # top point for heading
    y12 = 100
    # origo:
    x21 = roiWidth  # bottom point
    y21 = 200
    x22 = origo[0]  # circle center constantly changing
    y22 = origo[1]

    vector_1 = [x11 - x12, y11 - y12]
    vector_2 = [x21 - x22, y21 - y22]
    unit_vector_1 = vector_1 / np.linalg.norm(vector_1)
    unit_vector_2 = vector_2 / np.linalg.norm(vector_2)
    dot_product = np.dot(unit_vector_1, unit_vector_2)
    angle = np.arccos(dot_product)
    if x22 < x11 :
        angle = -1* angle
    # print("Angle :", angle * 180 / np.pi)
    angleTxt = str("%.1f" % round(angle * 180 / np.pi, 1))
    cv2.imshow('CIRCLE', frameCircle)
    cv2.moveWindow('CIRCLE',800,0)


# *** TRANSPARENT BOX ****************************************************
    # font which we will be using to display FPS 
    font = cv2.FONT_HERSHEY_PLAIN
    # time when we finish processing for this frame 
    new_frame_time = time.time() 
    fps = 1/(new_frame_time-prev_frame_time) 
    prev_frame_time = new_frame_time 
    fps = int(fps) 
    fps = "FPS: " + str(fps)
    # Trasparent rectangle below FTP text
    # First we crop the sub-rect from the image
    x, y, w, h = 0, 0, 250, 60
    sub_img = frame[y:y+h, x:x+w]
    white_rect = np.ones(sub_img.shape, dtype=np.uint8) * 200  #255
    res = cv2.addWeighted(sub_img, 0.5, white_rect, 0.5, 1.0)
    # Putting the image back to its position
    frame[y:y+h, x:x+w] = res


    frame[280:480, (320 - roiWidth):(320 + roiWidth)] = frameCircle
    frame = cv2.rectangle(frame, (320 - roiWidth, 280), (320 + roiWidth, 480), (255, 0, 0), 2) # big blue target window
    cv2.putText(frame, fps, (7, 15), font, 1, (0, 0, 0), 1, cv2.LINE_AA) 
    cv2.putText(frame, "Angle: " + angleTxt, (7, 35), font, 1, (0, 0, 0), 1, cv2.LINE_AA)
    cv2.putText(frame, "Radius & origo: " + str(rMax) + str(origo), (7, 55), font, 1, (0, 0, 0), 1,
                    cv2.LINE_AA)


# *** RED rectangulars   # origo = circle center
    aP1 = (320 - roiWidth + 1, 281)  # area Point 1
    aP2 = (320 - roiWidth + dangWidth, 281 + dangHeight)
    frame = cv2.rectangle(frame, aP1, aP2, (0, 0, 255), 1)  # 11,20
    if 320 - roiWidth + origo[0] > aP1[0] and 320 - roiWidth + origo[0] < aP2[0] and 280 + origo[1] > aP1[
        1] and 280 + origo[1] < aP2[1]:
        print("forward,50,20")
        print("RED left,50,20")
    bP1 = (320 + roiWidth - dangWidth, 281)
    bP2 = (320 + roiWidth - 1, 281 + dangHeight)
    frame = cv2.rectangle(frame, bP1, bP2, (0, 0, 255), 1)
    if 320 - roiWidth + origo[0] > bP1[0] and 320 - roiWidth + origo[0] < bP2[0] and 280 + origo[1] > bP1[
        1] and 280 + origo[1] < bP2[1]:
        print("forward,50,20")
        print("RED right,50,20")
   
# *** ORANGE rectangulars ****************************************************
    cP1 = (320 - roiWidth + 1, 281 + dangHeight)
    cP2 = (320 - roiWidth + dangWidth, 281 + 2 * dangHeight)
    frame = cv2.rectangle(frame, cP1, cP2, (0, 102, 255), 1)
    if 320 - roiWidth + origo[0] > cP1[0] and 320 - roiWidth + origo[0] < cP2[0] and 280 + origo[1] > cP1[
        1] and 280 + origo[1] < cP2[1]:
        print("forward,50,20")
        print("ORANGE left,50,20")
    dP1 = (320 + roiWidth - dangWidth, 281 + dangHeight)
    dP2 = (320 + roiWidth - 1, 281 + 2 * dangHeight)
    frame = cv2.rectangle(frame, dP1, dP2, (0, 102, 255), 1)
    if 320 - roiWidth + origo[0] > dP1[0] and 320 - roiWidth + origo[0] < dP2[0] and 280 + origo[1] > dP1[
            1] and 280 + origo[1] < dP2[1]:
        print("forward,50,20")
        print("ORANGE right,50,20")

# *** YELLOW rectangulars ****************************************************
    eP1 = (320 - roiWidth + 1, 281 + 2 * dangHeight)
    eP2 = (320 - roiWidth + dangWidth, 281 + 3 * dangHeight)
    frame = cv2.rectangle(frame, eP1, eP2, (0, 255, 255), 1)
    if 320 - roiWidth + origo[0] > eP1[0] and 320 - roiWidth + origo[0] < eP2[0] and 280 + origo[1] > eP1[
        1] and 280 + origo[1] < eP2[1]:
        print("forward,50,20")
        print("YELLOW left,50,20")
    fP1 = (320 + roiWidth - dangWidth, 281 + 2 * dangHeight)
    fP2 = (320 + roiWidth - 1, 281 + 3 * dangHeight)
    frame = cv2.rectangle(frame, fP1, fP2, (0, 255, 255), 1)
    if 320 - roiWidth + origo[0] > fP1[0] and 320 - roiWidth + origo[0] < fP2[0] and 280 + origo[1] > fP1[
            1] and 280 + origo[1] < fP2[1]:
        print("forward,50,20")
        print("YELLOW right,50,20")

# *** GREEEN rectangulars ****************************************************
    gP1 = (320 - roiWidth + 1, 281 + 3 * dangHeight)
    gP2 = (320 - roiWidth + dangWidth, 281 + 4 * dangHeight)
    frame = cv2.rectangle(frame, gP1, gP2, (0, 255, 0), 1)
    if 320 - roiWidth + origo[0] > gP1[0] and 320 - roiWidth + origo[0] < gP2[0] and 280 + origo[1] > gP1[
            1] and 280 + origo[1] < gP2[1]:
        print("forward,50,20")
        print("GREEEN left,50,20")
        #ser.write(bytes('YES\n','utf-8'))
        with serial.Serial('/dev/tty'+usb, 9600, timeout=10) as ser:
            #while True:
            ser.write(bytes('forward,50,20\n','utf-8'))
            ser.write(bytes('left,50,20\n','utf-8'))
        # print("Radius & origo: " + str(rMax) + str(origo))
    hP1 = (320 + roiWidth - dangWidth, 281 + 3 * dangHeight)
    hP2 = (320 + roiWidth - 1, 281 + 4 * dangHeight)
    frame = cv2.rectangle(frame, hP1, hP2, (0, 255, 0), 1)
    if 320 - roiWidth + origo[0] > hP1[0] and 320 - roiWidth + origo[0] < hP2[0] and 280 + origo[1] > hP1[
            1] and 280 + origo[1] < hP2[1]:
        print("forward,50,20")
        print("GREEEN right,50,20")
        with serial.Serial('/dev/tty'+usb, 9600, timeout=10) as ser:
            #while True:
            ser.write(bytes('forward,50,20\n','utf-8'))
            ser.write(bytes('right,50,20\n','utf-8'))
    
    pP1 = (320 - roiWidth + dangWidth, 281)
    pP2 = (320 + roiWidth - dangWidth, 480)
    if 320 - roiWidth + origo[0] > pP1[0] and 320 - roiWidth + origo[0] < pP2[0] and 280 + origo[1] > pP1[
            1] and 280 + origo[1] < pP2[1]:
        print("simple forward,50,20")
    # constant movement:
        with serial.Serial('/dev/tty'+usb, 9600, timeout=10) as ser:
            ser.write(bytes('forward,50,20\n','utf-8')) 

    cv2.imshow('FINAL', frame)
    cv2.moveWindow('FINAL',0,300)


cam.release()
cv2.destroyAllWindows()

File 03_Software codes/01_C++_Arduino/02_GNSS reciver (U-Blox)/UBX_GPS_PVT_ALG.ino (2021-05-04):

#include <SoftwareSerial.h>

// Connect the GPS RX/TX to arduino pins 3 and 5
SoftwareSerial serial = SoftwareSerial(3,5);

const unsigned char UBX_HEADER[]        = { 0xB5, 0x62 };
const unsigned char NAV_PVT_HEADER[] = { 0x01, 0x07 };
const unsigned char NAV_STATUS_HEADER[] = { 0x01, 0x03 };  /// !!!!!
const unsigned char ESF_ALG_HEADER[] = { 0x10, 0x14 }; 

enum _ubxMsgType {
  MT_NONE,
  MT_NAV_PVT,
  MT_NAV_STATUS
};

struct NAV_PVT {
  unsigned char cls;			// ID1
  unsigned char id;				// ID2
  unsigned short len;			// message length
  unsigned long iTOW;          // GPS time of week of the navigation epoch (ms)
  
  unsigned short year;         // Year (UTC) 
  unsigned char month;         // Month, range 1..12 (UTC)
  unsigned char day;           // Day of month, range 1..31 (UTC)
  unsigned char hour;          // Hour of day, range 0..23 (UTC)
  unsigned char minute;        // Minute of hour, range 0..59 (UTC)
  unsigned char second;        // Seconds of minute, range 0..60 (UTC)
  char valid;                  // Validity Flags (see graphic below)
  unsigned long tAcc;          // Time accuracy estimate (UTC) (ns)
  long nano;                   // Fraction of second, range -1e9 .. 1e9 (UTC) (ns)
  unsigned char fixType;       // GNSSfix Type, range 0..5
  char flags;                  // Fix Status Flags
  unsigned char reserved1;     // reserved
  unsigned char numSV;         // Number of satellites used in Nav Solution
  
  long lon;                    // Longitude (deg)
  long lat;                    // Latitude (deg)
  long height;                 // Height above Ellipsoid (mm)
  long hMSL;                   // Height above mean sea level (mm)
  unsigned long hAcc;          // Horizontal Accuracy Estimate (mm)
  unsigned long vAcc;          // Vertical Accuracy Estimate (mm)
  
  long velN;                   // NED north velocity (mm/s)
  long velE;                   // NED east velocity (mm/s)
  long velD;                   // NED down velocity (mm/s)
  long gSpeed;                 // Ground Speed (2-D) (mm/s)
  long heading;                // Heading of motion 2-D (deg)
  unsigned long sAcc;          // Speed Accuracy Estimate
  unsigned long headingAcc;    // Heading Accuracy Estimate
  unsigned short pDOP;         // Position dilution of precision
  short reserved2;             // Reserved
  unsigned long reserved3;     // Reserved
};

struct NAV_STATUS {
  unsigned char cls;
  unsigned char id;
  unsigned short len;
  unsigned long iTOW;
  unsigned char gpsFix;
  char flags;
  char fixStat;
  char flags2;
  unsigned long ttff;
  unsigned long msss;
};

struct ESF_ALG {
  unsigned char cls;		// ID1
  unsigned char id;			// ID2
  unsigned short len;		// message length
  unsigned long iTOW;		//U4 GPS time
  unsigned char version;   //U1
  unsigned char flags;			//U1
  unsigned char error;			//U1
  unsigned char res;				//U1
  unsigned long yaw;	//U4
  short pitch;	//I2
  short roll;	//I2
};


union UBXMessage {
  NAV_PVT navPvt;  // !!!!!!!!!!!
  NAV_STATUS navStatus;	// delete !!!!!!!!!!!
  ESF_ALG esfalg;
};

UBXMessage ubxMessage;

// The last two bytes of the message is a checksum value, used to confirm that the received payload is valid.
// The procedure used to calculate this is given as pseudo-code in the uBlox manual.
void calcChecksum(unsigned char* CK, int msgSize) {
  memset(CK, 0, 2);
  for (int i = 0; i < msgSize; i++) {
    CK[0] += ((unsigned char*)(&ubxMessage))[i];
    CK[1] += CK[0];
  }
}


// Compares the first two bytes of the ubxMessage struct with a specific message header.
// Returns true if the two bytes match.
boolean compareMsgHeader(const unsigned char* msgHeader) {
  unsigned char* ptr = (unsigned char*)(&ubxMessage);
  return ptr[0] == msgHeader[0] && ptr[1] == msgHeader[1];
}


// Reads in bytes from the GPS module and checks to see if a valid message has been constructed.
// Returns the type of the message found if successful, or MT_NONE if no message was found.
// After a successful return the contents of the ubxMessage union will be valid, for the 
// message type that was found. Note that further calls to this function can invalidate the
// message content, so you must use the obtained values before calling this function again.
int processGPS() {
  static int fpos = 0;
  static unsigned char checksum[2];
  
  static byte currentMsgType = MT_NONE;
  static int payloadSize = sizeof(UBXMessage);

  while ( serial.available() ) {
    
    byte c = serial.read();    
    //Serial.write(c);
    
    if ( fpos < 2 ) {
      // For the first two bytes we are simply looking for a match with the UBX header bytes (0xB5,0x62)
      if ( c == UBX_HEADER[fpos] )
        fpos++;
      else
        fpos = 0; // Reset to beginning state.
    }
    else {
      // If we come here then fpos >= 2, which means we have found a match with the UBX_HEADER
      // and we are now reading in the bytes that make up the payload.
      
      // Place the incoming byte into the ubxMessage struct. The position is fpos-2 because
      // the struct does not include the initial two-byte header (UBX_HEADER).
      if ( (fpos-2) < payloadSize )
        ((unsigned char*)(&ubxMessage))[fpos-2] = c;

      fpos++;
      
      if ( fpos == 4 ) {
        // We have just received the second byte of the message type header, 
        // so now we can check to see what kind of message it is.
        if ( compareMsgHeader(NAV_PVT_HEADER) ) {
          currentMsgType = MT_NAV_PVT;
          payloadSize = sizeof(NAV_PVT);
        }
        else if ( compareMsgHeader(ESF_ALG_HEADER) ) {
          currentMsgType = MT_ESF_ALGS;
          payloadSize = sizeof(ESF_ALG);
        }
        else {
          // unknown message type, bail
          fpos = 0;
          continue;
        }
      }
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

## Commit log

2020-06-24 Create servoPS4control
2020-06-25 Concept designs
    [profile_20X20.dxf]
2020-06-26 Servo code and connection
2020-11-02 Shield for Arduino MEGA
    PCB shield for Arduino MEGA (with Jetson Nano, UNO, XBee, radio contoller , 2xmotor contollers, 2xencoders etc. connetions).
    [PCB board-B_Cu.gbl, PCB board-B_Mask.gbs, PCB board-B_Paste.gbp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]
2020-11-02 Shield for Arduino MEGA
    Can be connected: Jetson Nano, radio contoller, 2xUART, 2xmotor contollers, 2xencoders with less wiring.
    [PCB board-B_Cu.gbl, PCB board-B_Mask.gbs, PCB board-B_Paste.gbp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]
2020-11-02 PCB board pictures
    Working :-) no smoke !
2021-05-04 Update
    New version
    [PCB board-B_Cu.gbl, PCB board-B_Mask.gbs, PCB board-B_Paste.gbp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]
2021-05-04 Upade
    new version
    [1x1 TH Vert 100mil.iges, 1x1 TH Vert 100mil.step, 1x10 TH Vert 100mil.iges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]
2021-05-04 Image recognition
    Codes for Jetson Nano
2021-05-05 Create chaos of wires_small.jpg
2021-05-07 Shield pdf drawings added
    Explanation how to use for ESC motor as well.
    [PCB board-B_Cu.gbl, PCB board-B_Mask.gbs, PCB board-B_Paste.gbp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]
2021-05-08 Update on ultrasonic sensor
2021-05-13 Create Robot Rover PCB Manual_v0.2.0.pptx
    PCB manual added
2021-06-18 LoRa breakout board
    LoRa breakout board
    [PCB LoRa 32-B_Cu.gbr, PCB LoRa 32-B_Mask.gbr, PCB LoRa 32-B_Paste.gbr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]

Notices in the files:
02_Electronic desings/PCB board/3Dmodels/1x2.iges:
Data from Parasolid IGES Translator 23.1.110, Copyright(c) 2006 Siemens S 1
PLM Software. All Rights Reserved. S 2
